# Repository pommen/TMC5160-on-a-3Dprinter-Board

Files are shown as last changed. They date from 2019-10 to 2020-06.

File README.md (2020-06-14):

# TMC5160 on a 3Dprinter Board
 TMC5160 using the pinheaders on a typical 3d printer controllerboard as inputs via an adapter board to a bigger general purpose tmc5160 50V 3-5A (Goal)

All files made in KICAD
(Work in progress)

todo:
bad footprint on RJ45 conn.
Clean up BOM (values and voltages)
74xx125 buffer footprint to wide
bigger fuse footprint (Automotive fuseholder?)
THT caps for H-bridge?
RJ45 pinout on silk?
clearer pin1 marking on 74xx125 buffers
Larger diameter holes on testpoints
I/O testpoints
Diag pin outputs

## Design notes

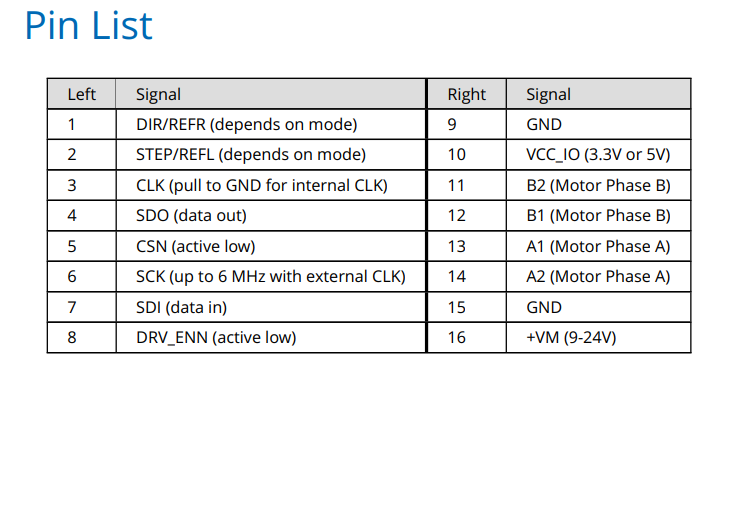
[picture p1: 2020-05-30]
Stepstick pinout.png

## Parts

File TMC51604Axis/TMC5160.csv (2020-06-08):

Id | Designator | Package | Quantity | Designation | Supplier and ref
1 | C37 | C_0805_peter | 1 | 15pF
2 | TP2,TP1 | TestPoint_Pad_D1.5mm | 2 | TestPoint
3 | TP7 | TestPoint_THTPad_1.5x1.5mm_Drill0.7mm | 1 | TestPoint
4 | R52,R51,R27,R16 | R_1206_3216Metric | 4 | 0R1
5 | C47,C46,C45,C44,C43 | C_0805_peter | 5 | 100n
6 | R50 | R_0805_peter | 1 | 20R
7 | C8 | C_2010_5025Metric_Pad1.52x2.65mm_HandSolder | 1 | 47u/25
8 | TP6,TP5,TP4 | TestPoint_Pad_1.5x1.5mm | 3 | TestPoint
9 | C42 | C_0805_peter | 1 | 10u
10 | U3 | LQFP-48-1EP_7x7mm_P0.5mm_EP3.6x3.6mm_peter | 1 | TMC5160A-TA
11 | C34,C9,C27,C33,C41 | C_0603_1608Metric | 5 | 100n
12 | R18,R3 | R_0805_peter | 2 | 100k
13 | R19 | R_0805_peter | 1 | NC
14 | U4 | Oscillator_SMD_Abracon_ASDMB-4Pin_2.5x2.0mm | 1 | ASDMB-12.0MHz
15 | J4 | TerminalBlock_Phoenix_PT-1,5-3-3.5-H_1x03_P3.50mm_Horizontal | 1 | EncCon1
16 | U5,U7,U6 | SO-14_5.3x10.2mm_P1.27mm | 3 | 74LVC125
17 | D27,D29,D28,D26,D25,D24,D23,D22,D21,D20 | SOT-23 | 10 | BAT54S
18 | R49,R48,R40,R39,R38,R37,R36,R35,R34,R33 | R_0805_peter | 10 | 100R
19 | R47,R46,R45,R44,R43,R42,R41,R32,R31,R6 | R_0805_peter | 10 | 2k2
20 | R7 | R_0805_peter | 1 | 1R
21 | R4 | R_0805_peter | 1 | 10K
22 | R5 | R_0805_peter | 1 | 4K12
23 | R2 | R_0805_peter | 1 | 36K5
24 | TP3 | TestPoint_THTPad_1.0x1.0mm_Drill0.5mm | 1 | spare
25 | C18 | C_0805_peter | 1 | 100n/100V
26 | C14 | C_0805_peter | 1 | 22nF
27 | C13 | C_0805_peter | 1 | 220p
28 | C12 | C_0805_peter | 1 | 100p
29 | C11 | C_0805_peter | 1 | 1uF
30 | C6 | C_0805_peter | 1 | 2.2uF
31 | C5 | C_0805_peter | 1 | 47nF
32 | C2 | C_0805_peter | 1 | 10p
33 | C1 | C_0805_peter | 1 | 330n
34 | C10 | C_0603_1608Metric | 1 | 10u
35 | C17 | C_0603_1608Metric | 1 | 22n/100v
36 | C19 | C_0603_1608Metric | 1 | 220n/100v
37 | C22,C24,C26,C35,C36 | C_0603_1608Metric | 5 | 470n
38 | C23 | C_0603_1608Metric | 1 | 2.2uF
39 | C25 | C_0603_1608Metric | 1 | 2.2u
40 | C32,C40 | C_0603_1608Metric | 2 | 2n2
41 | C28,C29,C30,C31 | C_0603_1608Metric | 4 | 1n/100V
42 | U2 | SOT-223-3_TabPin2 | 1 | LM2937
43 | U1 | SOT-23-5_HandSoldering | 1 | AP2210-3.3V
44 | R30,R29 | R_0603_1608Metric | 2 | 100K
45 | R28,R26,R17,R15 | R_0603_1608Metric | 4 | 47R
46 | R25,R24,R23,R22,R14,R13,R11,R10 | R_0603_1608Metric | 8 | 12R
47 | R21,R20,R12,R9 | R_0603_1608Metric | 4 | 0R
48 | R8 | R_0603_1608Metric | 1 | 2R2
49 | R1 | R_2512_6332Metric | 1 | 0R01
50 | Q4 | SOT-23 | 1 | BSS138
51 | Q3,Q2 | V-DFN5045-12 | 2 | DMHT6016LFJ
52 | Q1 | TO-252-2 | 1 | SUD08P06-155L
53 | L1 | L_7.3x7.3_H3.5 | 1 | 33uH
54 | JP3 | SolderJumper-3_P2.0mm_Open_TrianglePad1.0x1.5mm | 1 | Encoder_Voltage_Sel
55 | JP2 | SolderJumper-3_P2.0mm_Open_TrianglePad1.0x1.5mm | 1 | SD_MODE
56 | JP1 | SolderJumper-3_P2.0mm_Open_TrianglePad1.0x1.5mm | 1 | SPI_MODE
57 | J6 | TerminalBlock_Phoenix_PT-1,5-3-3.5-H_1x03_P3.50mm_Horizontal | 1 | EncCon2
58 | J5,J3 | 360s-1812-11001(RJ45) | 2 | RJ45_Shielded
59 | J2 | TerminalBlock_Phoenix_PT-1,5-4-3.5-H_1x04_P3.50mm_Horizontal | 1 | Stepper_conn
60 | J1 | PhoenixContact_MSTB_2,5_2-GF_1x02_P5.00mm_Horizontal_ThreadedFlange_MountHole | 1 | +48Vin
61 | H4,H3,H2,H1 | MountingHole_3.2mm_M3 | 4 | MountingHole
62 | FB2 | R_0805_2012Metric_Pad1.15x1.40mm_HandSolder | 1 | MPZ2012S601A
63 | F1 | Fuse_2512_6332Metric | 1 | Fuse
64 | D19,D18,D17,D16,D15,D14,D13,D12,D11 | D_0805__HandSolder_peter | 9 | LED
65 | D10,D9,D8,D7 | SOT-23 | 4 | ZHCS1006TA
66 | D6 | D_SOD-123F | 1 | D_Schottky
67 | D5 | TSSOP-16-1EP_4.4x5mm_P0.65mm | 1 | LT1766
68 | D4 | D_0805_2012Metric | 1 | LED
69 | D3 | D_1206_3216Metric | 1 | 10V
70 | D2 | D_1206_3216Metric | 1 | 7V
71 | D1 | D_SOD-123 | 1 | 1N4148W
72 | C39,C21 | CP_Elec_10x14.3 | 2 | 220uF/100V
73 | C38,C20 | C_1206_3216Metric | 2 | 470n/100V
74 | C16 | C_1210_3225Metric_Pad1.42x2.65mm_HandSolder | 1 | 4,7uF/100v
75 | C15 | C_1210_3225Metric_Pad1.42x2.65mm_HandSolder | 1 | 100n/100v
76 | C7 | CP_Radial_D10.0mm_P5.00mm | 1 | 47u/25V
77 | C4 | CP_Elec_8x6.2 | 1 | 22uF/100v
78 | C3 | CP_Elec_8x6.2 | 1 | 10uF/100v

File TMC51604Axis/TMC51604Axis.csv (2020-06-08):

Source: | E:\GitHub\TMC5160 on a 3Dprinter Board\TMC5160-on-a-3Dprinter-Board\TMC51604Axis\TMC51604Axis.sch
Date: | 06/01/20 14:39:34
Tool: | Eeschema (5.1.6)-1
Generator: | C:\Program Files\KiCad\bin\scripting\plugins/bom_csv_grouped_by_value_with_fp.py
Component Count: | 162
Ref | Qnty | Value | Cmp name | Footprint | Description | Vendor
C1, | 1 | 330n | C_Small | peters:C_0805_peter | Unpolarized capacitor, small symbol
C2, | 1 | 10p | C_Small | peters:C_0805_peter | Unpolarized capacitor, small symbol
C3, | 1 | 10uF/100v | CP | Capacitor_SMD:CP_Elec_8x6.2 | Polarized capacitor
C4, | 1 | 22uF/100v | C | Capacitor_SMD:CP_Elec_8x6.2 | Unpolarized capacitor
C5, | 1 | 47nF | C | peters:C_0805_peter | Unpolarized capacitor
C6, | 1 | 2.2uF | C | peters:C_0805_peter | Unpolarized capacitor
C7, | 1 | 47u/25V | CP | Capacitor_THT:CP_Radial_D10.0mm_P5.00mm | Polarized capacitor
C8, | 1 | 47u/25 | C | Capacitor_SMD:C_2010_5025Metric_Pad1.52x2.65mm_HandSolder | Unpolarized capacitor
C9, C27, C33, C34, C41, | 5 | 100n | C_Small | Capacitor_SMD:C_0603_1608Metric | Unpolarized capacitor, small symbol
C10, | 1 | 10u | C | Capacitor_SMD:C_0603_1608Metric | Unpolarized capacitor
C11, | 1 | 1uF | C | peters:C_0805_peter | Unpolarized capacitor
C12, | 1 | 100p | C | peters:C_0805_peter | Unpolarized capacitor
C13, | 1 | 220p | C | peters:C_0805_peter | Unpolarized capacitor
C14, | 1 | 22nF | C_Small | peters:C_0805_peter | Unpolarized capacitor, small symbol
C15, | 1 | 100n/100v | C_Small | Capacitor_SMD:C_1210_3225Metric_Pad1.42x2.65mm_HandSolder | Unpolarized capacitor, small symbol
C16, | 1 | 4,7uF/100v | C_Small | Capacitor_SMD:C_1210_3225Metric_Pad1.42x2.65mm_HandSolder | Unpolarized capacitor, small symbol
C17, | 1 | 22n/100v | C_Small | Capacitor_SMD:C_0603_1608Metric | Unpolarized capacitor, small symbol
C18, | 1 | 100n/100V | C_Small | peters:C_0805_peter | Unpolarized capacitor, small symbol
C19, | 1 | 220n/100v | C_Small | Capacitor_SMD:C_0603_1608Metric | Unpolarized capacitor, small symbol
C20, C38, | 2 | 470n/100V | C | Capacitor_SMD:C_1206_3216Metric | Unpolarized capacitor
C21, C39, | 2 | 220uF/100V | CP | Capacitor_SMD:CP_Elec_10x14.3 | Polarized capacitor
C22, C24, C26, C35, C36, | 5 | 470n | C_Small | Capacitor_SMD:C_0603_1608Metric | Unpolarized capacitor, small symbol
C23, | 1 | 2.2uF | C_Small | Capacitor_SMD:C_0603_1608Metric | Unpolarized capacitor, small symbol
C25, | 1 | 2.2u | C_Small | Capacitor_SMD:C_0603_1608Metric | Unpolarized capacitor, small symbol
C28, C29, C30, C31, | 4 | 1n/100V | C | Capacitor_SMD:C_0603_1608Metric | Unpolarized capacitor
C32, C40, | 2 | 2n2 | C_Small | Capacitor_SMD:C_0603_1608Metric | Unpolarized capacitor, small symbol
C37, | 1 | 15pF | C | peters:D_0805_peter | Unpolarized capacitor
C42, | 1 | 10u | C | peters:C_0805_peter | Unpolarized capacitor
C43, C44, C45, C46, C47, | 5 | 100n | C | peters:C_0805_peter | Unpolarized capacitor
D1, | 1 | 1N4148W | 1N4148W | Diode_SMD:D_SOD-123 | 75V 0.15A Fast Switching Diode, SOD-123
D2, | 1 | 7V | D_Zener | Diode_SMD:D_1206_3216Metric | Zener diode
D3, | 1 | 10V | D_Zener | Diode_SMD:D_1206_3216Metric | Zener diode
D4, | 1 | LED | LED | Diode_SMD:D_0805_2012Metric | Light emitting diode
D5, | 1 | LT1766 | LT1766 | Package_SO:TSSOP-16-1EP_4.4x5mm_P0.65mm | 5.5V to 60V 1.5A, 200kHz Step-Down Switching Regulator
D6, | 1 | D_Schottky | D_Schottky | Diode_SMD:D_SOD-123F | Schottky diode
D7, D8, D9, D10, | 4 | ZHCS1006TA | ZHCS1006TA | Package_TO_SOT_SMD:SOT-23
D11, D12, D13, D14, D15, D16, D17, D18, D19, | 9 | LED | LED | peters:D_0805__HandSolder_peter | Light emitting diode
D20, D21, D22, D23, D24, D25, D26, D27, D28, D29, | 10 | BAT54S | BAT54S | Package_TO_SOT_SMD:SOT-23 | schottky barrier diode
F1, | 1 | Fuse | Fuse | Fuse:Fuse_2512_6332Metric | Fuse
FB2, | 1 | MPZ2012S601A | Ferrite_Bead | Resistor_SMD:R_0805_2012Metric_Pad1.15x1.40mm_HandSolder | Ferrite bead
H1, H2, H3, H4, | 4 | MountingHole | MountingHole | MountingHole:MountingHole_3.2mm_M3 | Mounting Hole without connection
J1, | 1 | +48Vin | Conn_01x02_Female | Connector_Phoenix_MSTB:PhoenixContact_MSTB_2,5_2-GF_1x02_P5.00mm_Horizontal_ThreadedFlange_MountHole | Generic connector, single row, 01x02, script generated (kicad-library-utils/schlib/autogen/connector/)
J2, | 1 | Stepper_conn | Screw_Terminal_01x04 | TerminalBlock_Phoenix:TerminalBlock_Phoenix_PT-1,5-4-3.5-H_1x04_P3.50mm_Horizontal | Generic screw terminal, single row, 01x04, script generated (kicad-library-utils/schlib/autogen/connector/)
J3, J5, | 2 | RJ45_Shielded | RJ45_Shielded | peters:360s-1812-11001(RJ45) | RJ connector, 8P8C (8 positions 8 connected), Shielded
J4, | 1 | EncCon1 | Screw_Terminal_01x03 | TerminalBlock_Phoenix:TerminalBlock_Phoenix_PT-1,5-3-3.5-H_1x03_P3.50mm_Horizontal | Generic screw terminal, single row, 01x03, script generated (kicad-library-utils/schlib/autogen/connector/)
J6, | 1 | EncCon2 | Screw_Terminal_01x03 | TerminalBlock_Phoenix:TerminalBlock_Phoenix_PT-1,5-3-3.5-H_1x03_P3.50mm_Horizontal | Generic screw terminal, single row, 01x03, script generated (kicad-library-utils/schlib/autogen/connector/)
JP1, | 1 | SPI_MODE | Jumper_NC_Dual | Jumper:SolderJumper-3_P2.0mm_Open_TrianglePad1.0x1.5mm | Dual jumper, normally closed
JP2, | 1 | SD_MODE | Jumper_NC_Dual | Jumper:SolderJumper-3_P2.0mm_Open_TrianglePad1.0x1.5mm | Dual jumper, normally closed
JP3, | 1 | Encoder_Voltage_Sel | Jumper_3_Bridged12 | Jumper:SolderJumper-3_P2.0mm_Open_TrianglePad1.0x1.5mm | Jumper, 3-pole, pins 1+2 closed/bridged
L1, | 1 | 33uH | L | Inductor_SMD:L_7.3x7.3_H3.5 | Inductor
Q1, | 1 | SUD08P06-155L | SUD08P06-155L | Package_TO_SOT_SMD:TO-252-2 | 8.4A Id, 60V Vds, TrenchFET P-Channel Power MOSFET, 155mOhm Ron, 19nC Qg, -55 to 150 °C, TO-252-2
Q2, Q3, | 2 | DMHT6016LFJ | DMHT6016LFJ | Libs:V-DFN5045-12 | 60V N-CHANNEL ENHANCEMENT MODE MOSFET H-BRIDGE
Q4, | 1 | BSS138 | BSS138 | Package_TO_SOT_SMD:SOT-23 | 50V Vds, 0.22A Id, N-Channel MOSFET, SOT-23
R1, | 1 | 0R01 | R | Resistor_SMD:R_2512_6332Metric | Resistor
R2, | 1 | 36K5 | R_Small | peters:R_0805_peter | Resistor, small symbol
R3, R18, | 2 | 100k | R | peters:R_0805_peter | Resistor
R4, | 1 | 10K | R | peters:R_0805_peter | Resistor
R5, | 1 | 4K12 | R_Small | peters:R_0805_peter | Resistor, small symbol
R6, R31, R32, R41, R42, R43, R44, R45, R46, R47, | 10 | 2k2 | R | peters:R_0805_peter | Resistor
R7, | 1 | 1R | R_Small | peters:R_0805_peter | Resistor, small symbol
R8, | 1 | 2R2 | R_Small | Resistor_SMD:R_0603_1608Metric | Resistor, small symbol
R9, R12, R20, R21, | 4 | 0R | R_Small | Resistor_SMD:R_0603_1608Metric | Resistor, small symbol
R10, R11, R13, R14, R22, R23, R24, R25, | 8 | 12R | R_Small | Resistor_SMD:R_0603_1608Metric | Resistor, small symbol
R15, R17, R26, R28, | 4 | 47R | R | Resistor_SMD:R_0603_1608Metric | Resistor
R16, R27, R51, R52, | 4 | 0R1 | R | Resistor_SMD:R_1206_3216Metric | Resistor
R19, | 1 | NC | R | peters:R_0805_peter | Resistor
R29, R30, | 2 | 100K | R_Small | Resistor_SMD:R_0603_1608Metric | Resistor, small symbol
R33, R34, R35, R36, R37, R38, R39, R40, R48, R49, | 10 | 100R | R | peters:R_0805_peter | Resistor
R50, | 1 | 20R | R | peters:R_0805_peter | Resistor
TP1, TP2, | 2 | TestPoint | TestPoint | TestPoint:TestPoint_Pad_D1.5mm | test point
TP3, | 1 | spare | TestPoint | TestPoint:TestPoint_THTPad_1.0x1.0mm_Drill0.5mm | test point
TP4, TP5, TP6, | 3 | TestPoint | TestPoint | TestPoint:TestPoint_Pad_1.5x1.5mm | test point
TP7, | 1 | TestPoint | TestPoint | TestPoint:TestPoint_THTPad_1.5x1.5mm_Drill0.7mm | test point
U1, | 1 | AP2210-3.3V | AP2210-3.3V | Package_TO_SOT_SMD:SOT-23-5_HandSoldering | AP2210 Series 3.3 V 300 mA Surface Mount RF ULDO Regulator - SOT-23-5
U2, | 1 | LM2937 | LM2937 | Package_TO_SOT_SMD:SOT-223-3_TabPin2 | LM2937 500-mA Low Dropout Regulator
U3, | 1 | TMC5160A-TA | TMC5160A-TA | peters:LQFP-48-1EP_7x7mm_P0.5mm_EP3.6x3.6mm_peter | The TMC5160 is a high power stepper motor controller and driver IC with serial communication interfaces
U4, | 1 | ASDMB-12.0MHz | ASDMB-xxxMHz | Oscillator:Oscillator_SMD_Abracon_ASDMB-4Pin_2.5x2.0mm | 1.8-3.3V SMD Ultra Miniature Crystal Clock Oscillator, Abracon
U5, U6, U7, | 3 | 74LVC125 | 74LVC125 | Package_SO:SO-14_5.3x10.2mm_P1.27mm | Quad buffer 3-State outputs

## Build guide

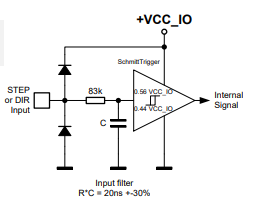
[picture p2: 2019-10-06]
step dir schmitt trig.png

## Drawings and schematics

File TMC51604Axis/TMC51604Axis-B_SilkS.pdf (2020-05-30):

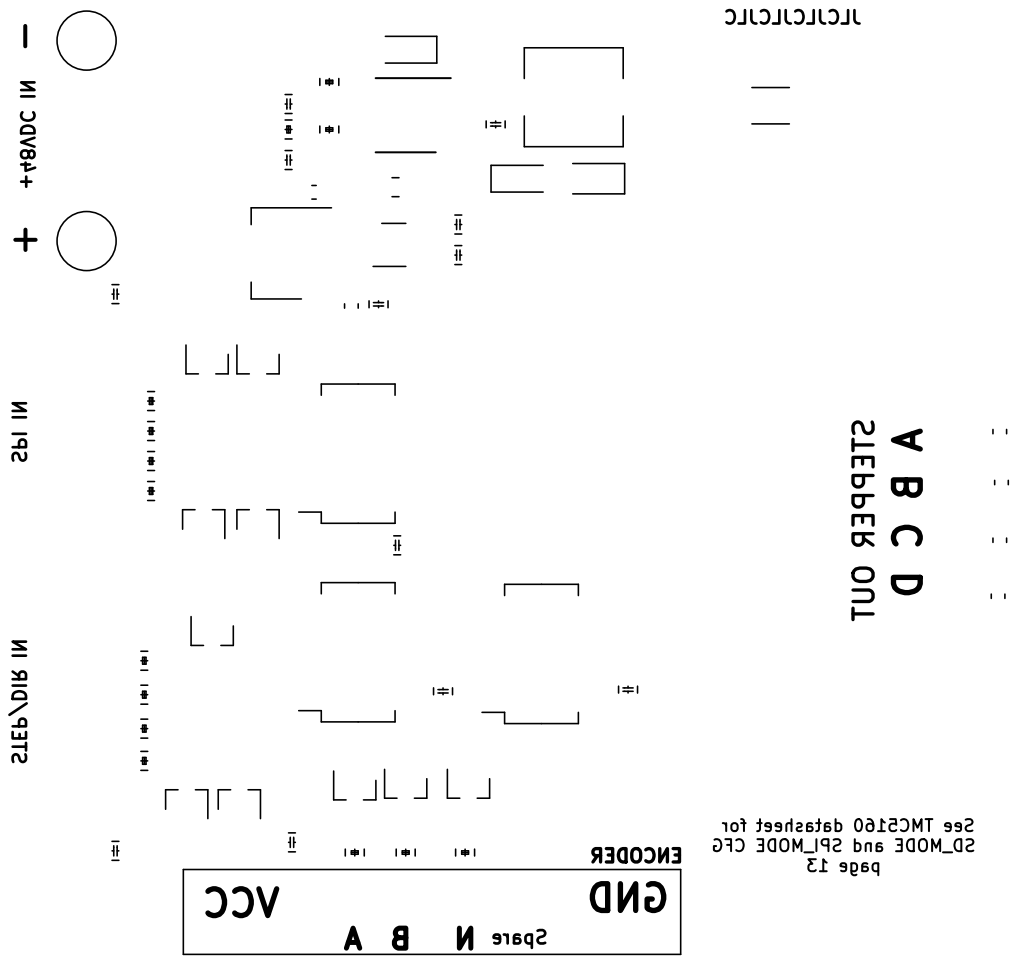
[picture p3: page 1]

page 13 - + GND A B N Spare VCC

ENCODER STEP/DIR IN SPI IN +48VDC IN D C B STEPPER OUT A

See TMC5160 datasheet for SD_MODE and SPI_MODE CFG

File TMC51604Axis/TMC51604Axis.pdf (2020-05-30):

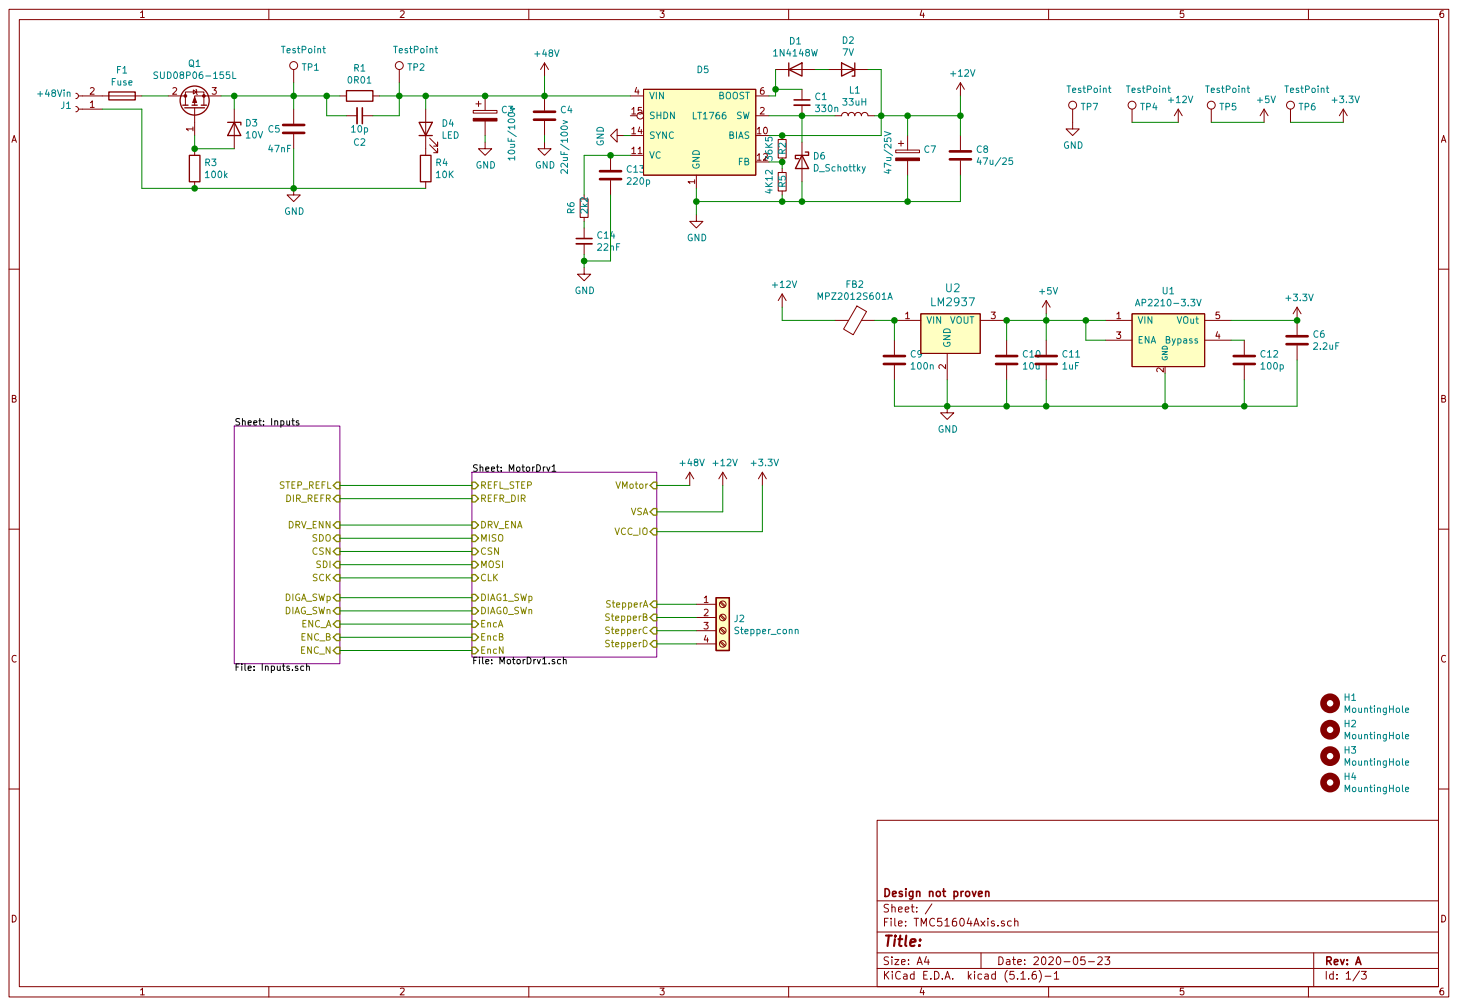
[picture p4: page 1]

1 BIAS 10 VC 11 FB 12 SYNC 14 SHDN 15 SW 2 VIN 4 BOOST 6 D5
TP6 TestPoint C13

2 ENA 3 Bypass 4 VOut 5 U1 AP2210-3.3V GND

Sheet: Inputs
Sheet: MotorDrv1 File: MotorDrv1.sch CLK MOSI MISO
VMotor REFR_DIR

Id: 1/3 Title: File: TMC51604Axis.sch Sheet: / Design not proven

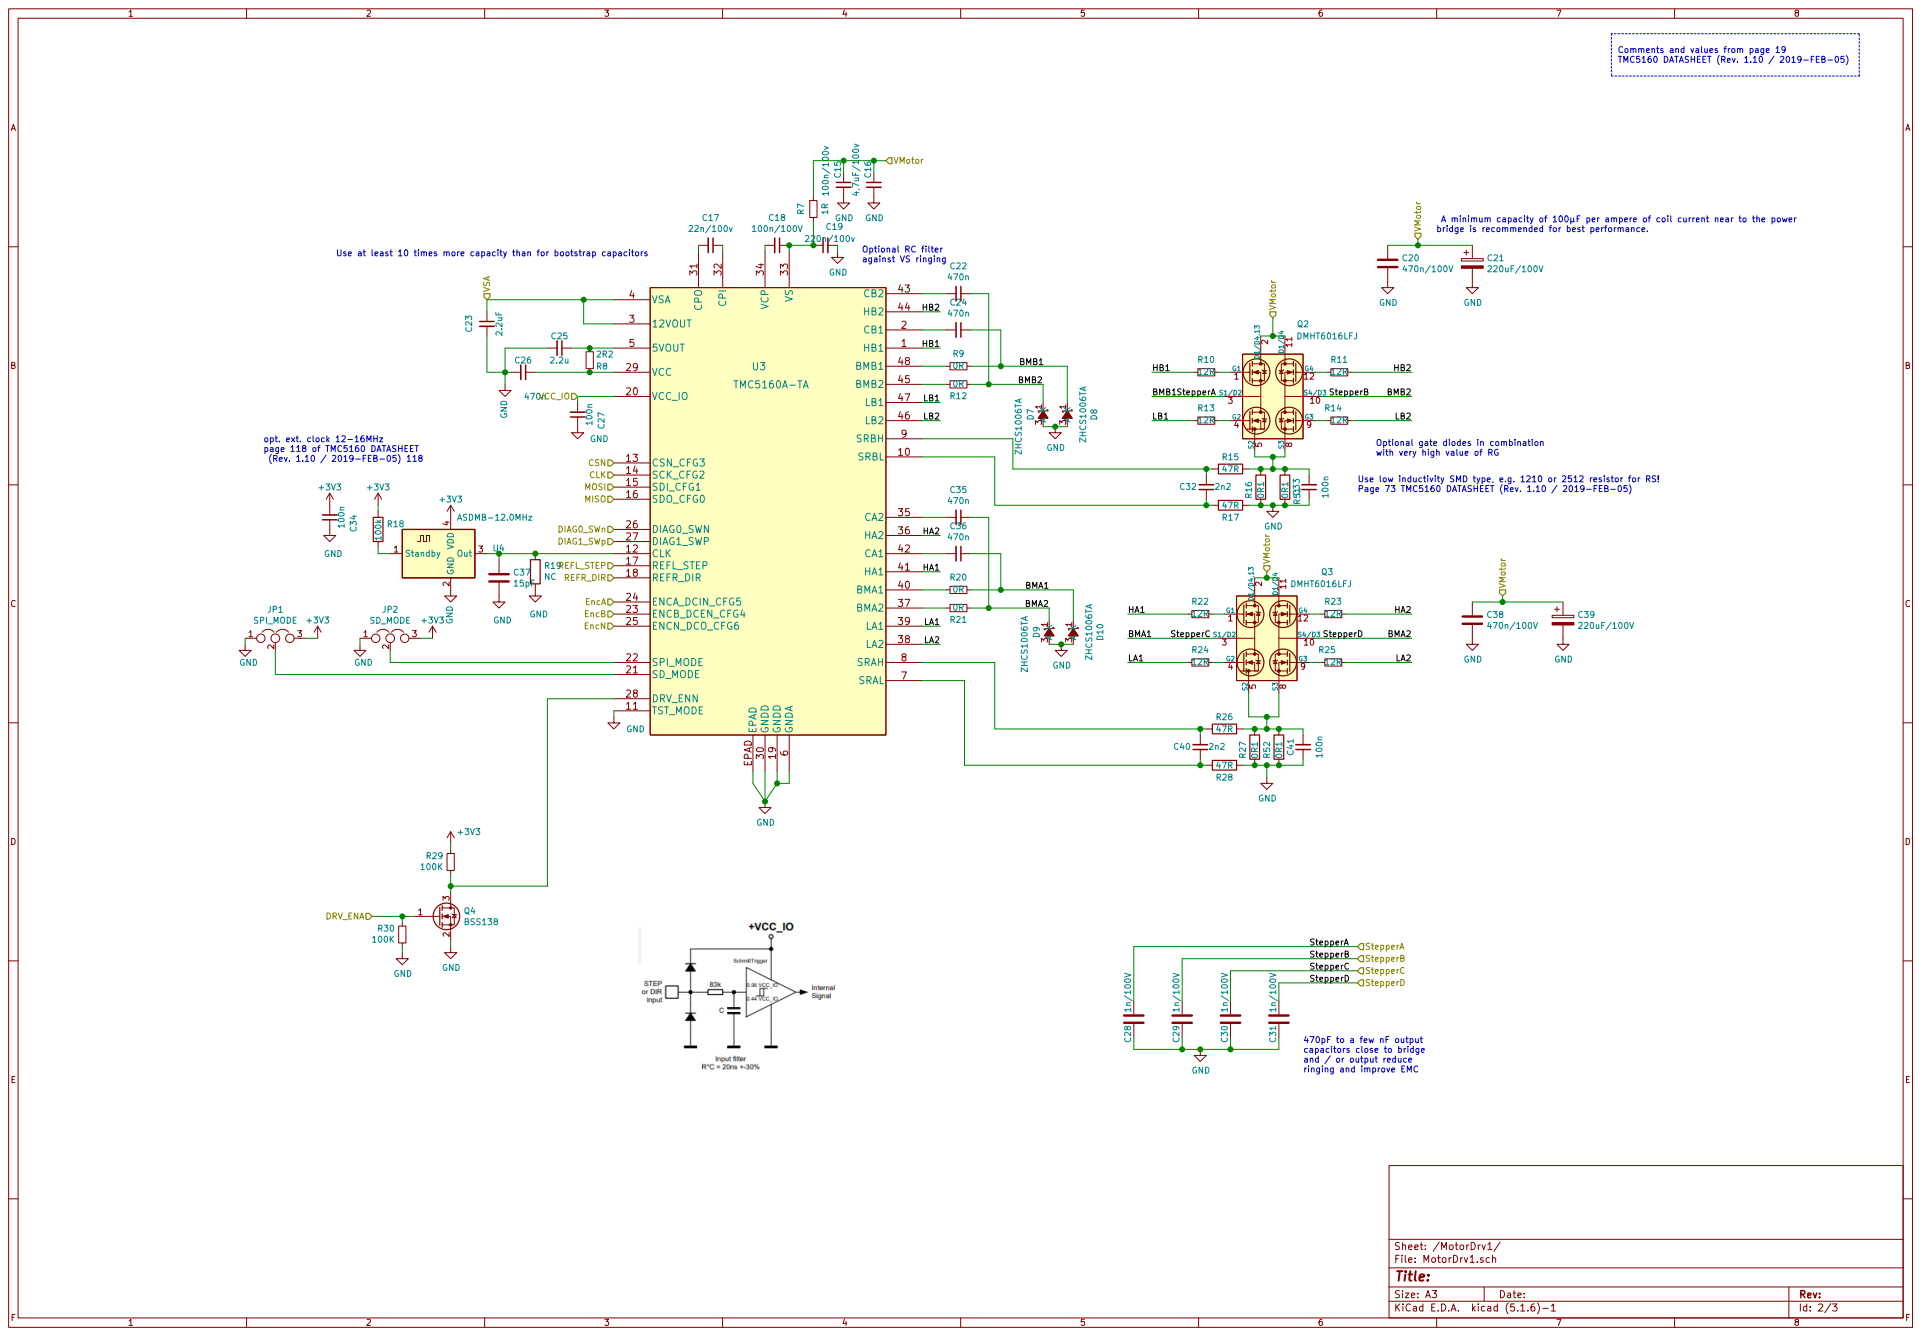
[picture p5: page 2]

Comments and values from page 19
TMC5160 DATASHEET (Rev. 1.10 / 2019-FEB-05)

6 SRAL 7 SRAH 8 SRBH 9 EPAD EPAD U3 TMC5160A-TA C15 100n/100v GND C41 100n

A minimum capacity of 100µF per ampere of coil current near to the power
bridge is recommended for best performance.

Use at least 10 times more capacity than for bootstrap capacitors

Optional gate diodes in combination
with very high value of RG

Page 73 TMC5160 DATASHEET (Rev. 1.10 / 2019-FEB-05)

470pF to a few nF output
capacitors close to bridge
and / or output reduce
ringing and improve EMC

Id: 2/3 Title: File: MotorDrv1.sch Sheet: /MotorDrv1/

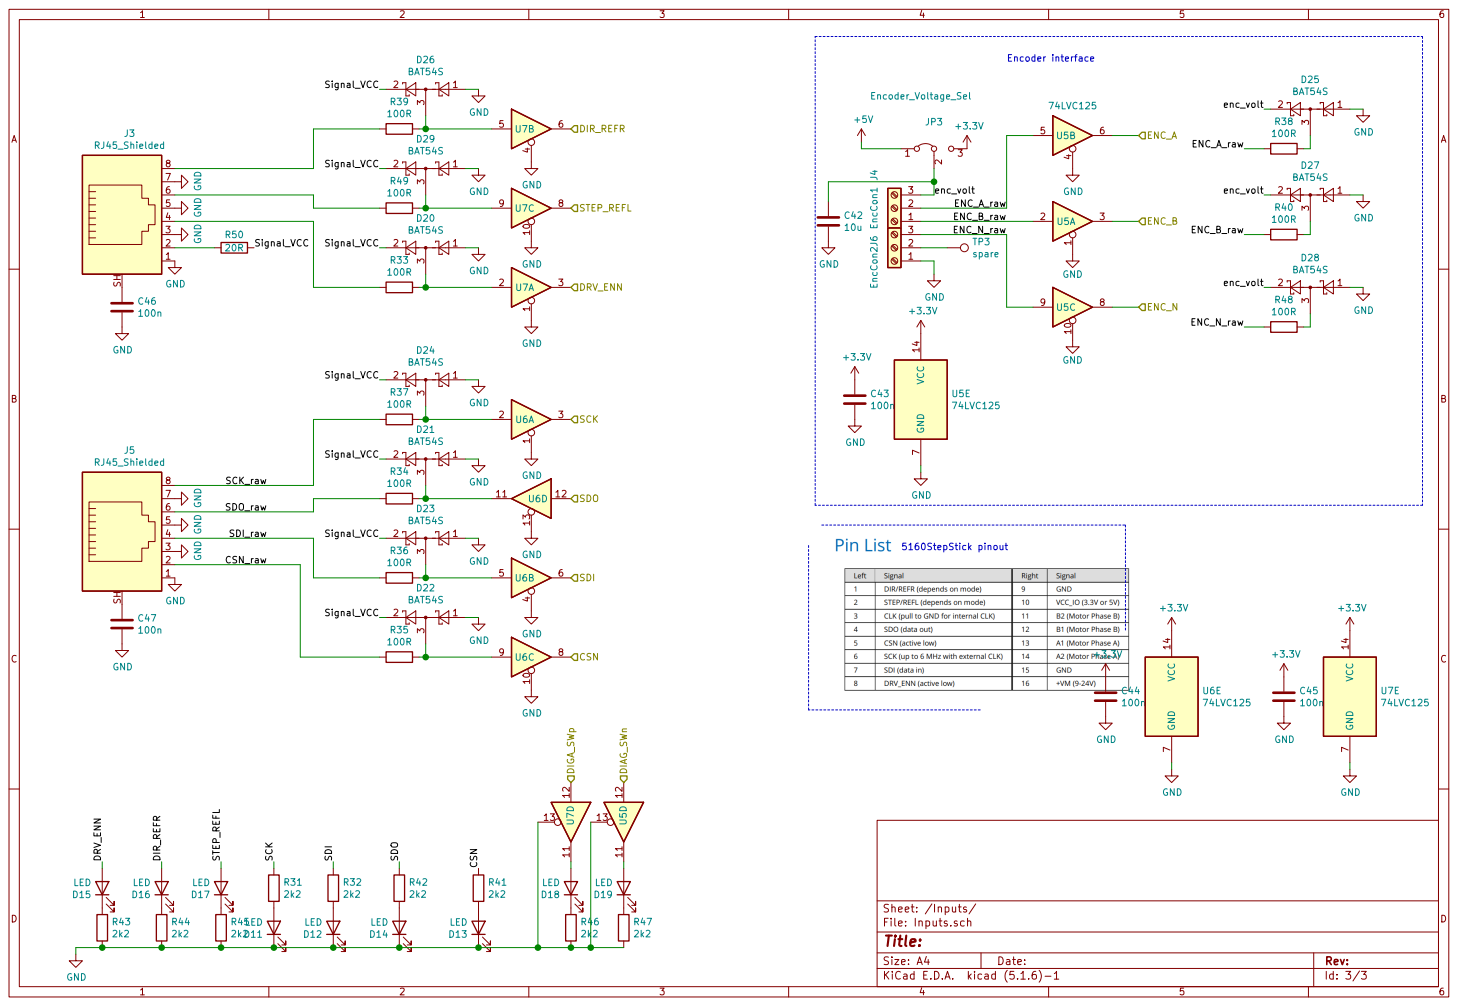
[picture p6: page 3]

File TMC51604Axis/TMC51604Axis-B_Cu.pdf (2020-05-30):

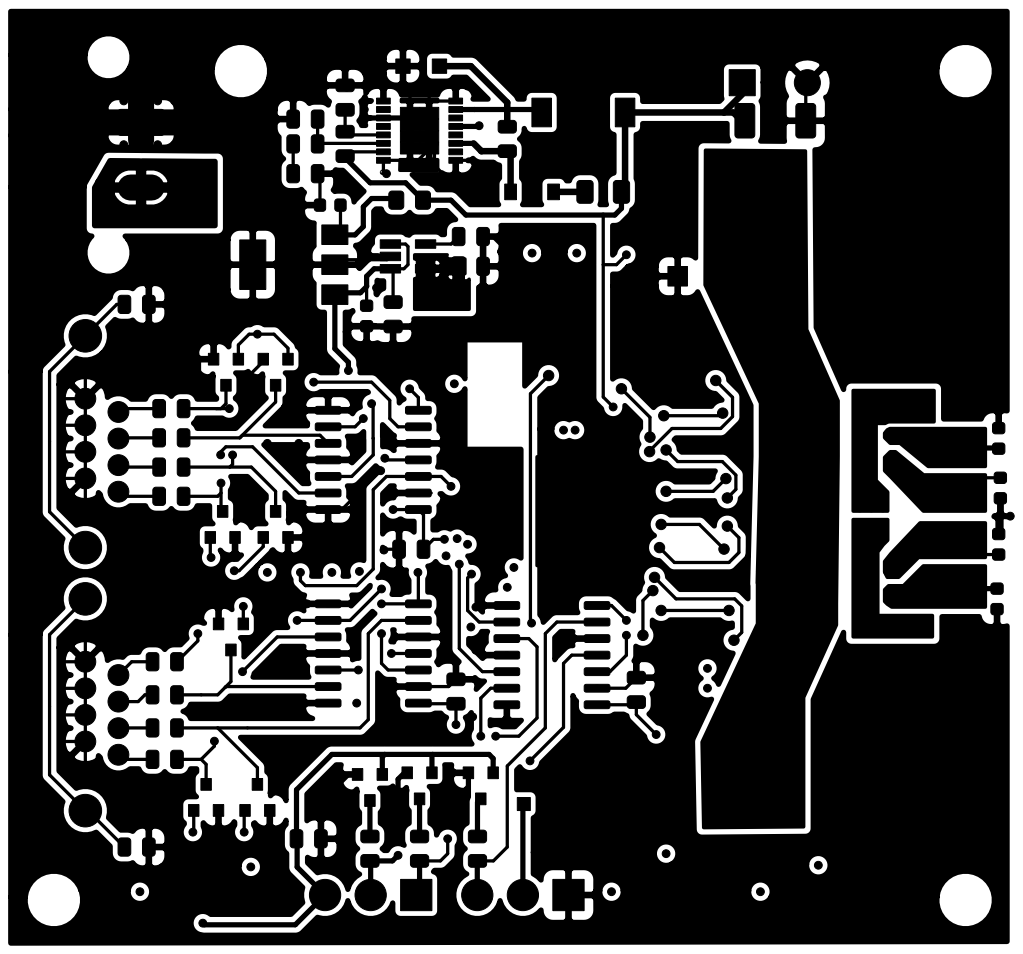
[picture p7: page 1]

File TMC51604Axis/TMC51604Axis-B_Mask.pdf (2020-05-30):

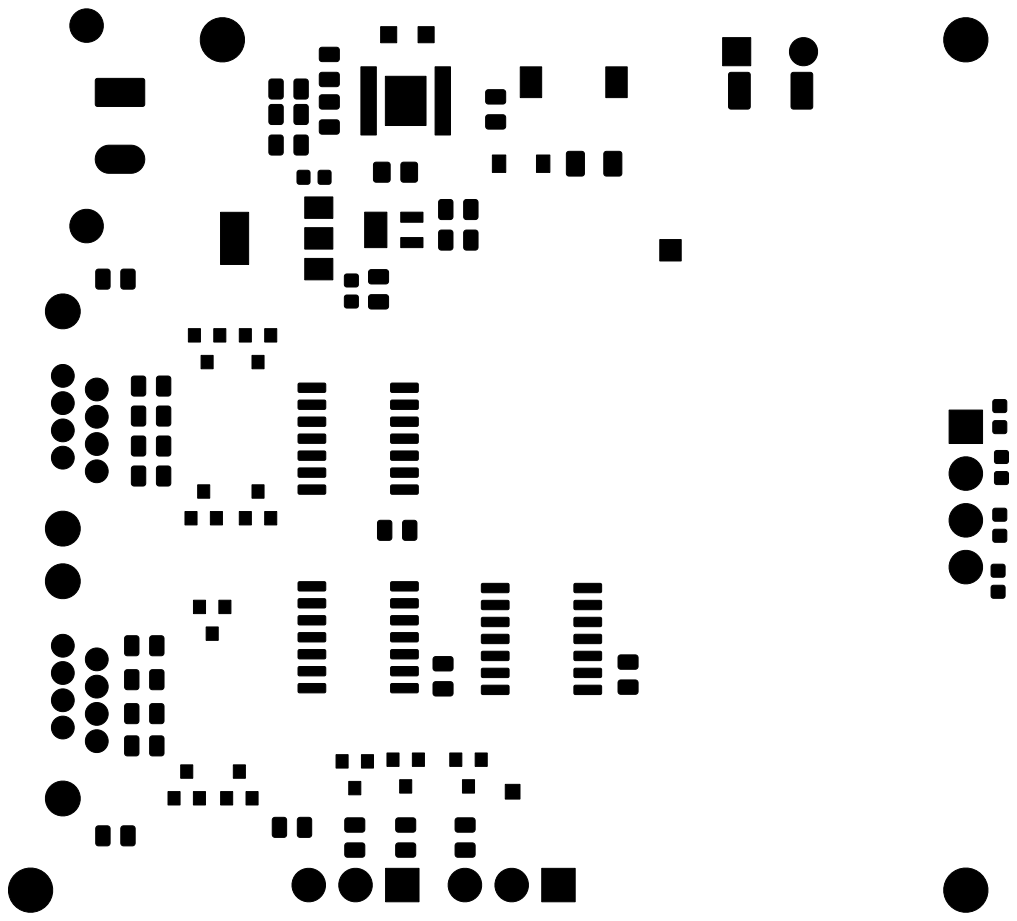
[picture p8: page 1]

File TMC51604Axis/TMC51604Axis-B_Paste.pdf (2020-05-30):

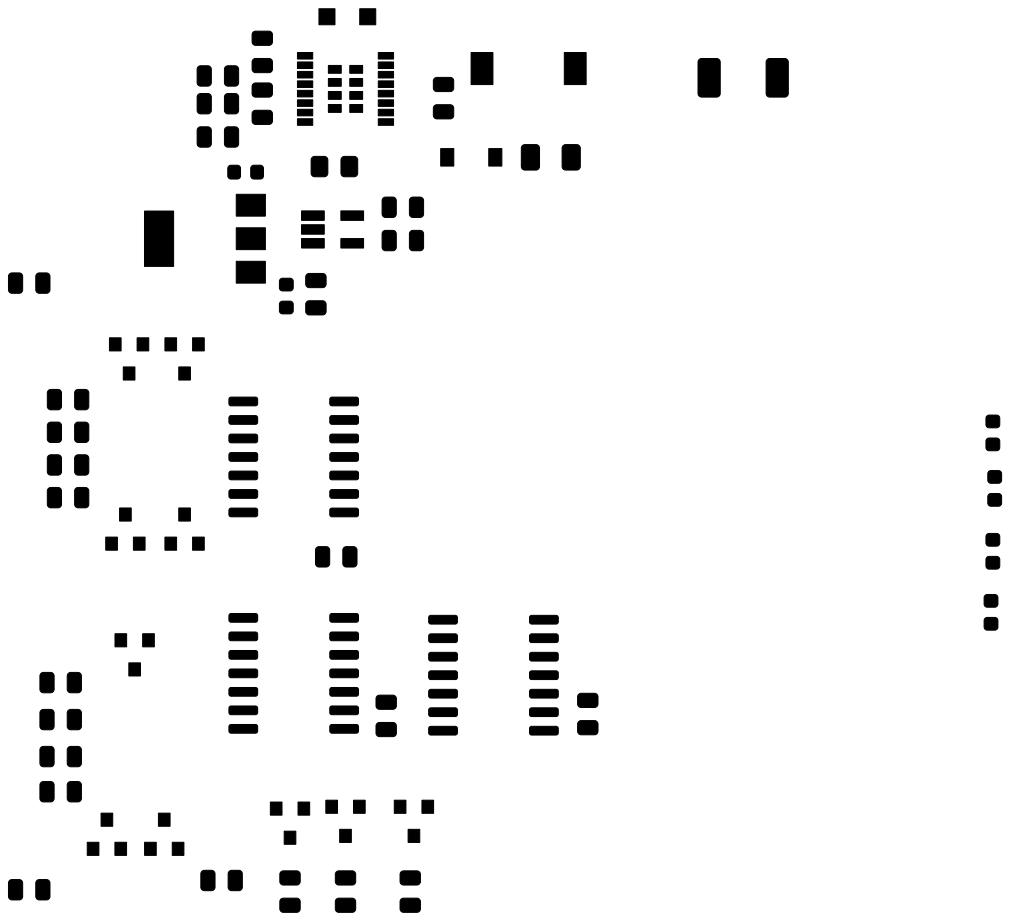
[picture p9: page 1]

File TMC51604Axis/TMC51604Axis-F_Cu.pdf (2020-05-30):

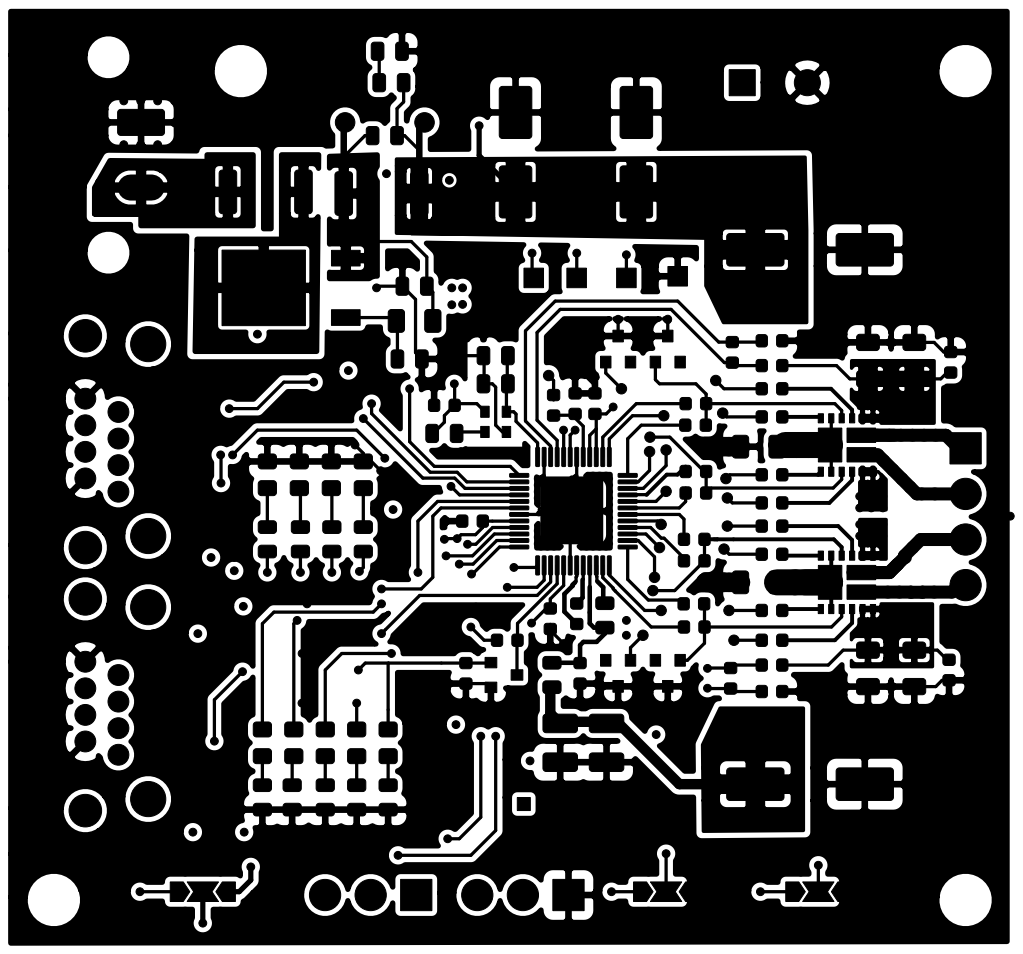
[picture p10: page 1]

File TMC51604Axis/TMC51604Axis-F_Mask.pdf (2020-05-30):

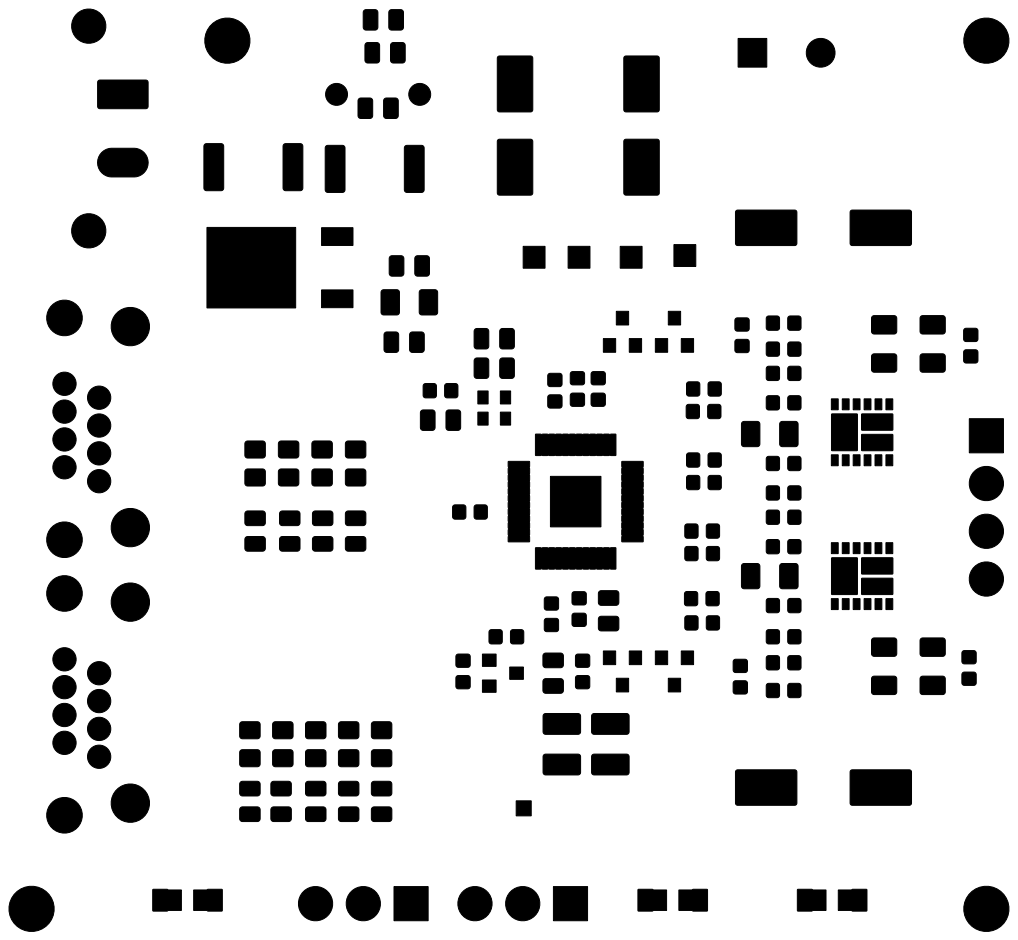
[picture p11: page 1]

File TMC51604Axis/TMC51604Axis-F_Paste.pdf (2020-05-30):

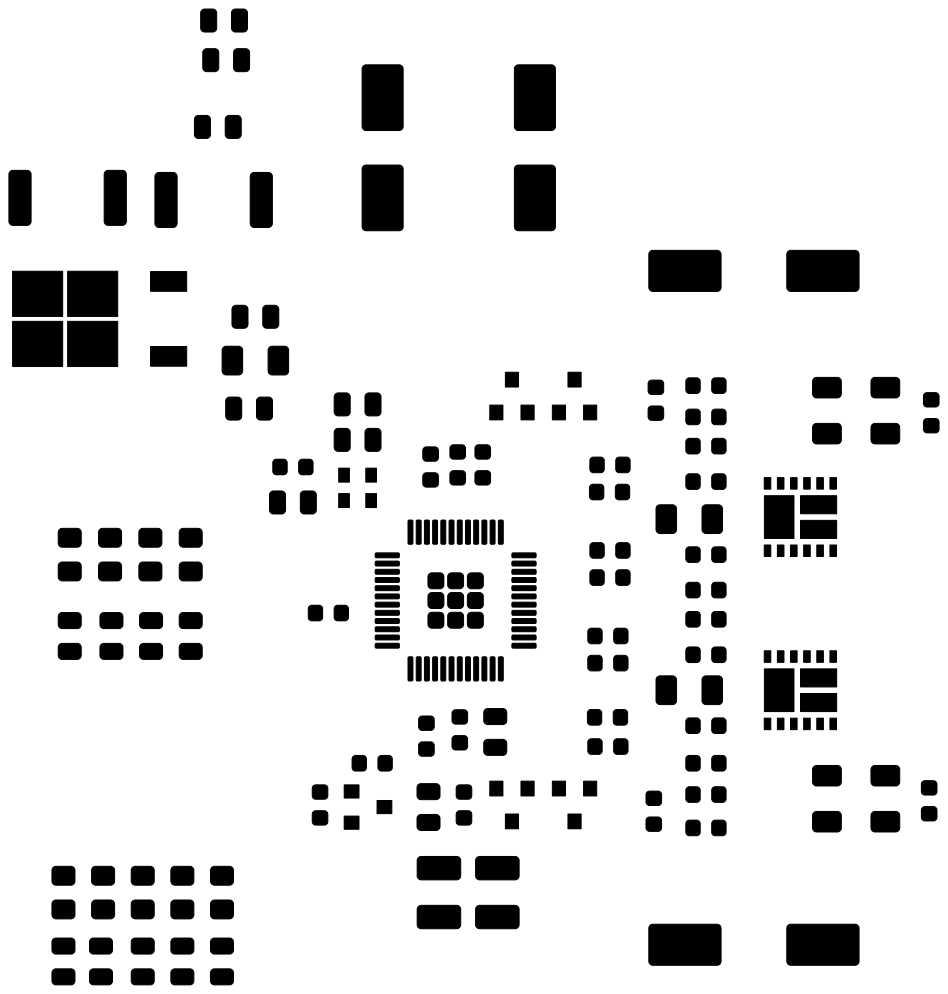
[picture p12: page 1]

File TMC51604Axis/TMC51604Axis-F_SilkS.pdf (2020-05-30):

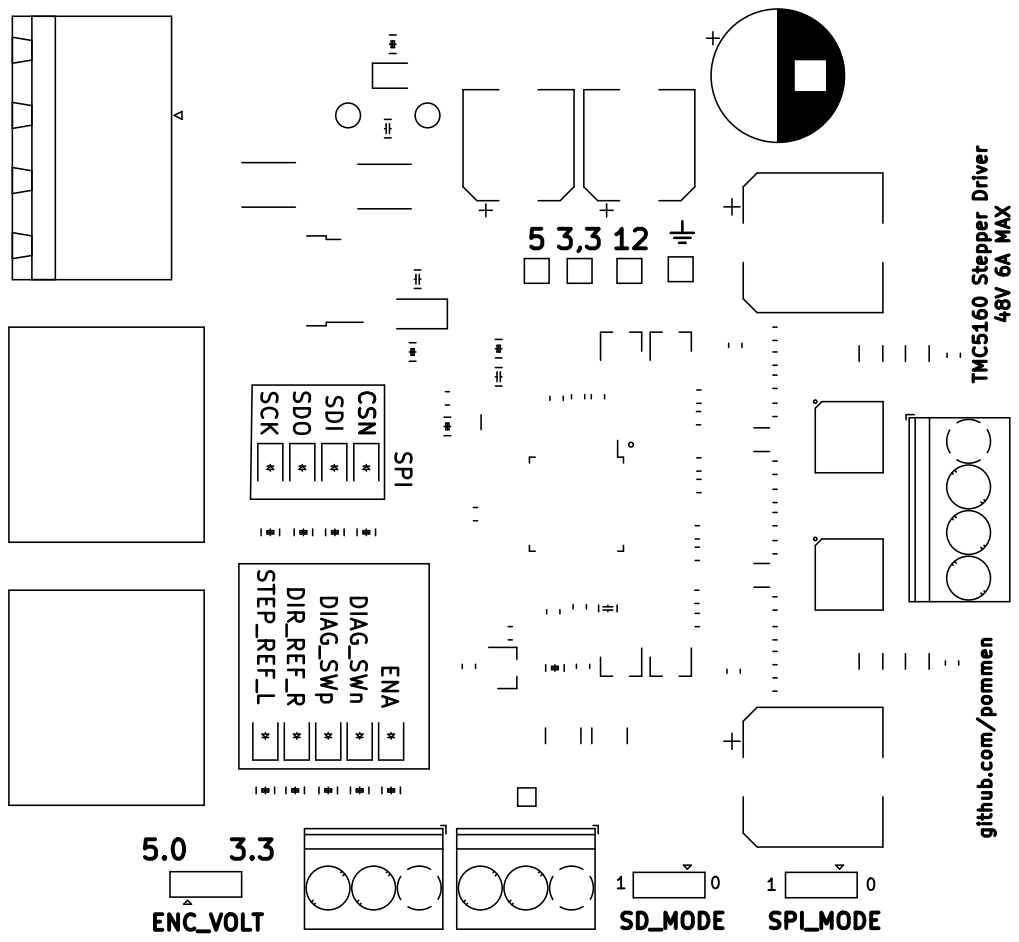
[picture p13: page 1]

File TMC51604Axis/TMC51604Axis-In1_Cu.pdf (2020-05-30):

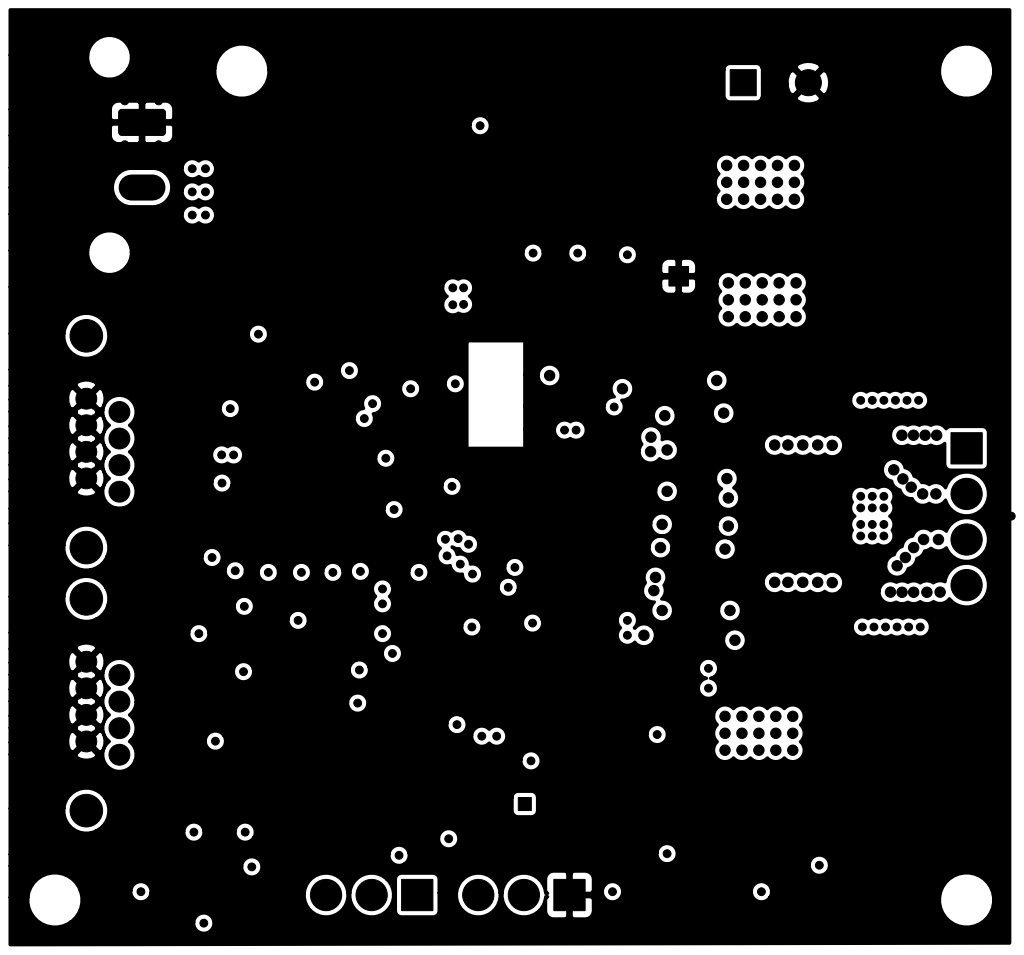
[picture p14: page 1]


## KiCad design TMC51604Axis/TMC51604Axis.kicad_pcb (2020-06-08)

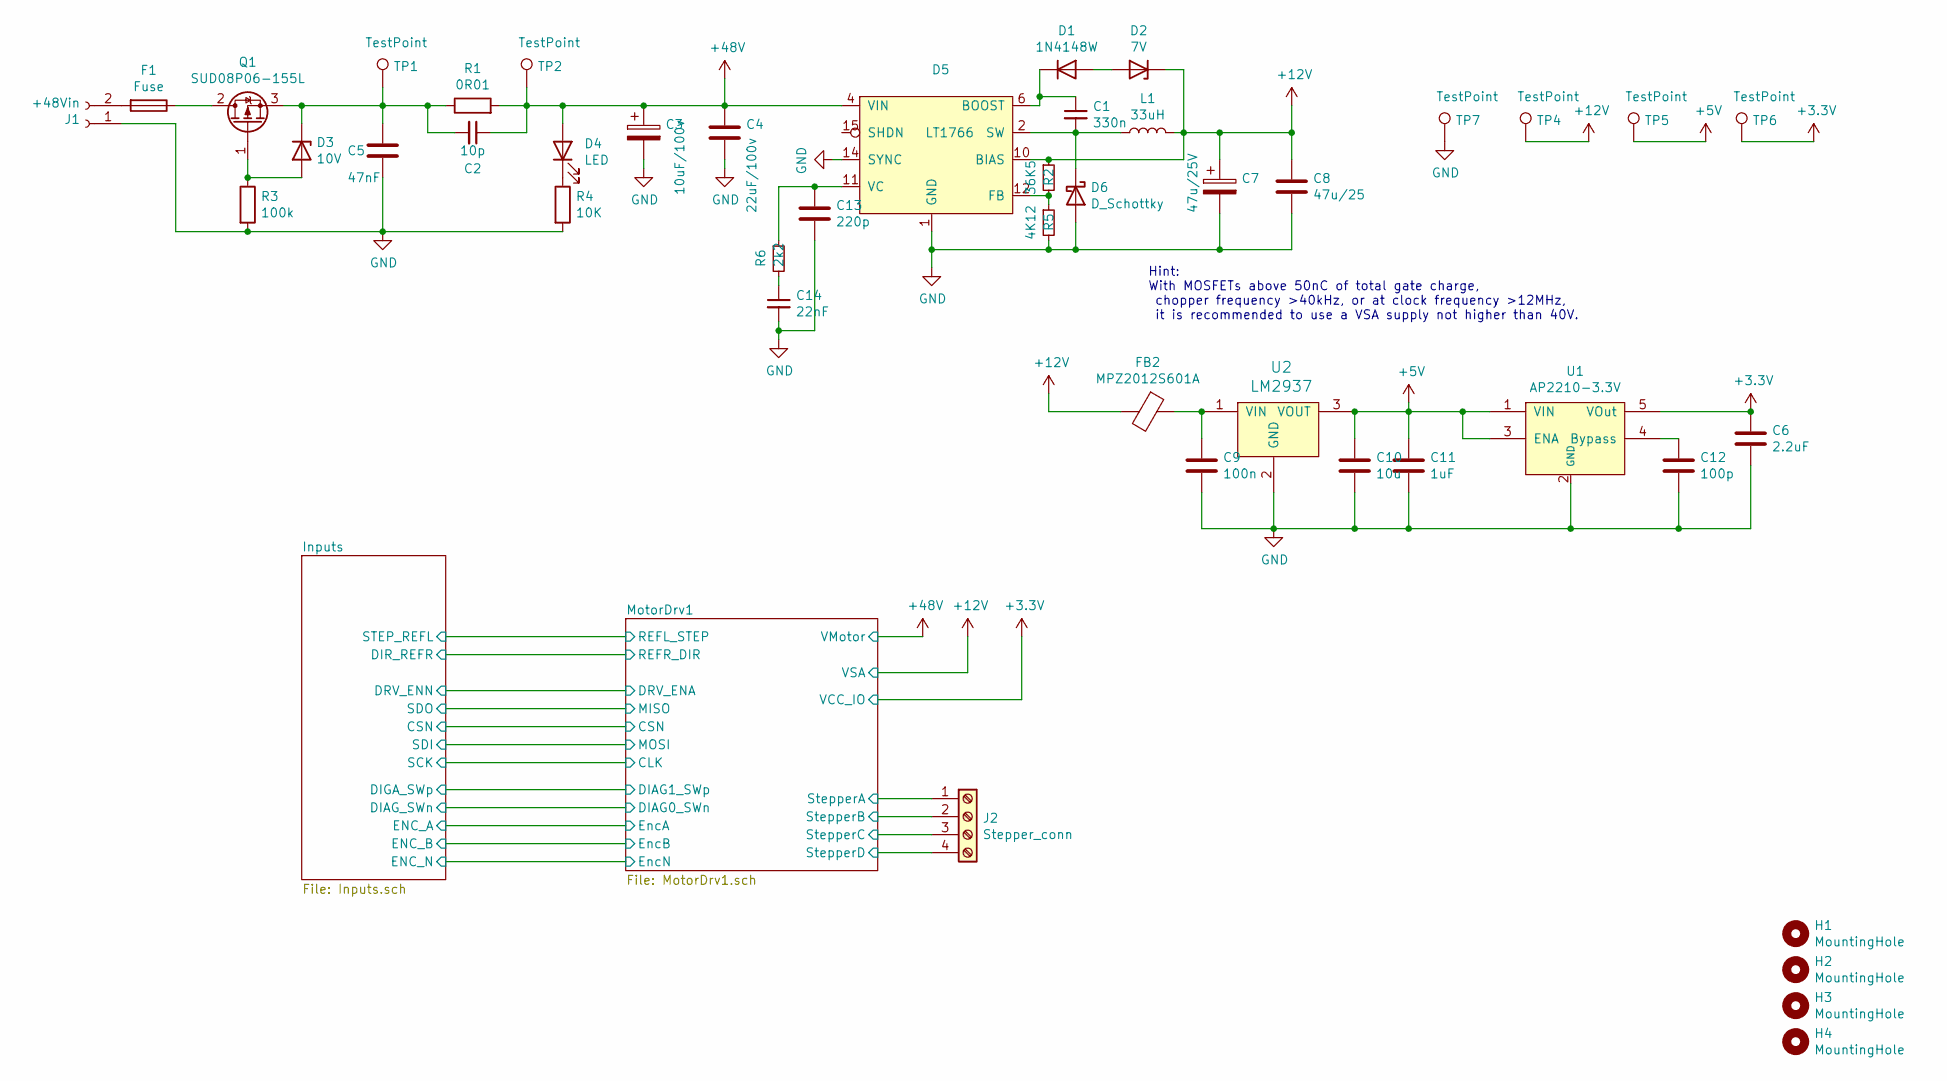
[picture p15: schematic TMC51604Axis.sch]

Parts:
C1: 330n; C_0805_peter
C2: 10p; C_0805_peter
C3: 10uF/100v; CP_Elec_8x6.2
C4: 22uF/100v; CP_Elec_8x6.2
C5: 47nF; C_0805_peter
C6: 2.2uF; C_0805_peter
C7: 47u/25V; CP_Radial_D10.0mm_P5.00mm
C8: 47u/25; C_2010_5025Metric_Pad1.52x2.65mm_HandSolder
C9: 100n; C_0603_1608Metric
C10: 10u; C_0603_1608Metric
C11: 1uF; C_0805_peter
C12: 100p; C_0805_peter
C13: 220p; C_0805_peter
C14: 22nF; C_0805_peter
D1: 1N4148W; D_SOD-123
D2: 7V; D_1206_3216Metric
D3: 10V; D_1206_3216Metric
D4: LED; D_0805_2012Metric
D5: LT1766; TSSOP-16-1EP_4.4x5mm_P0.65mm
D6: D_Schottky; D_SOD-123F
F1: Fuse; Fuse_2512_6332Metric
FB2: MPZ2012S601A; R_0805_2012Metric_Pad1.15x1.40mm_HandSolder
H1, H2, H3, H4: MountingHole; MountingHole_3.2mm_M3
J1: +48Vin; PhoenixContact_MSTB_2,5_2-GF_1x02_P5.00mm_Horizontal_Thread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
J2: Stepper_conn; TerminalBlock_Phoenix_PT-1,5-4-3.5-H_1x04_P3.50mm_Horizontal
L1: 33uH; L_7.3x7.3_H3.5
Q1: SUD08P06-155L; TO-252-2
R1: 0R01; R_2512_6332Metric
R2: 36K5; R_0805_peter
R3: 100k; R_0805_peter
R4: 10K; R_0805_peter
R5: 4K12; R_0805_peter
R6: 2k2; R_0805_peter
TP1, TP2: TestPoint; TestPoint_Pad_D1.5mm
TP4, TP5, TP6: TestPoint; TestPoint_Pad_1.5x1.5mm
TP7: TestPoint; TestPoint_THTPad_1.5x1.5mm_Drill0.7mm
U1: AP2210-3.3V; SOT-23-5_HandSoldering
U2: LM2937; SOT-223-3_TabPin2

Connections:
+5V: C10.1, C11.1, TP5.1, U1.1 (VIN), U1.3 (ENA), U2.3 (VOUT); also elsewhere on the board
+12V: C7.1, C8.1, D2.1 (K), D5.10 (BIAS), FB2.2, L1.2, R2.1, TP4.1; also elsewhere on the board
+48V: C2.1, C3.1, C4.1, D4.2 (A), D5.4 (VIN), R1.2, TP2.1; also elsewhere on the board
/MotorDrv1/StepperA: J2.1; also elsewhere on the board
/MotorDrv1/StepperB: J2.2; also elsewhere on the board
/MotorDrv1/StepperC: J2.3; also elsewhere on the board
/MotorDrv1/StepperD: J2.4; also elsewhere on the board
GND: C3.2, C4.2, C5.2, C6.2, C7.2, C8.2, C9.2, C10.2, C11.2, C12.2, C13.2, C14.2, D5.1 (GND), D5.8 (GND), D5.9 (GND), D5.14 (SYNC), D5.16 (GND), D5.17 (GND), D6.2 (A), J1.1, R3.2, R4.2, R5.2, TP7.1, U1.2 (GND), U2.2 (GND); also elsewhere on the board
unnamed: C1.1, D1.1 (K), D5.6 (BOOST)
unnamed: C1.2, D5.2 (SW), D6.1 (K), L1.1
unnamed: C2.2, C5.1, D3.1 (K), Q1.3 (S), R1.1, TP1.1
unnamed: C9.1, FB2.1, U2.1 (VIN)
unnamed: C12.1, U1.4 (Bypass)
unnamed: C13.1, D5.11 (VC), R6.1
unnamed: C14.1, R6.2
unnamed: D1.2 (A), D2.2 (A)
unnamed: D3.2 (A), Q1.1 (G), R3.1
unnamed: D4.1 (K), R4.1
unnamed: D5.12 (FB), R2.2, R5.1
unnamed: F1.1, Q1.2 (D)
unnamed: F1.2, J1.2

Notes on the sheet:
Hint: With MOSFETs above 50nC of total gate charge, chopper frequency >40kHz, or at clock frequency >12MHz, it is recommended to use a VSA supply not higher than 40V.

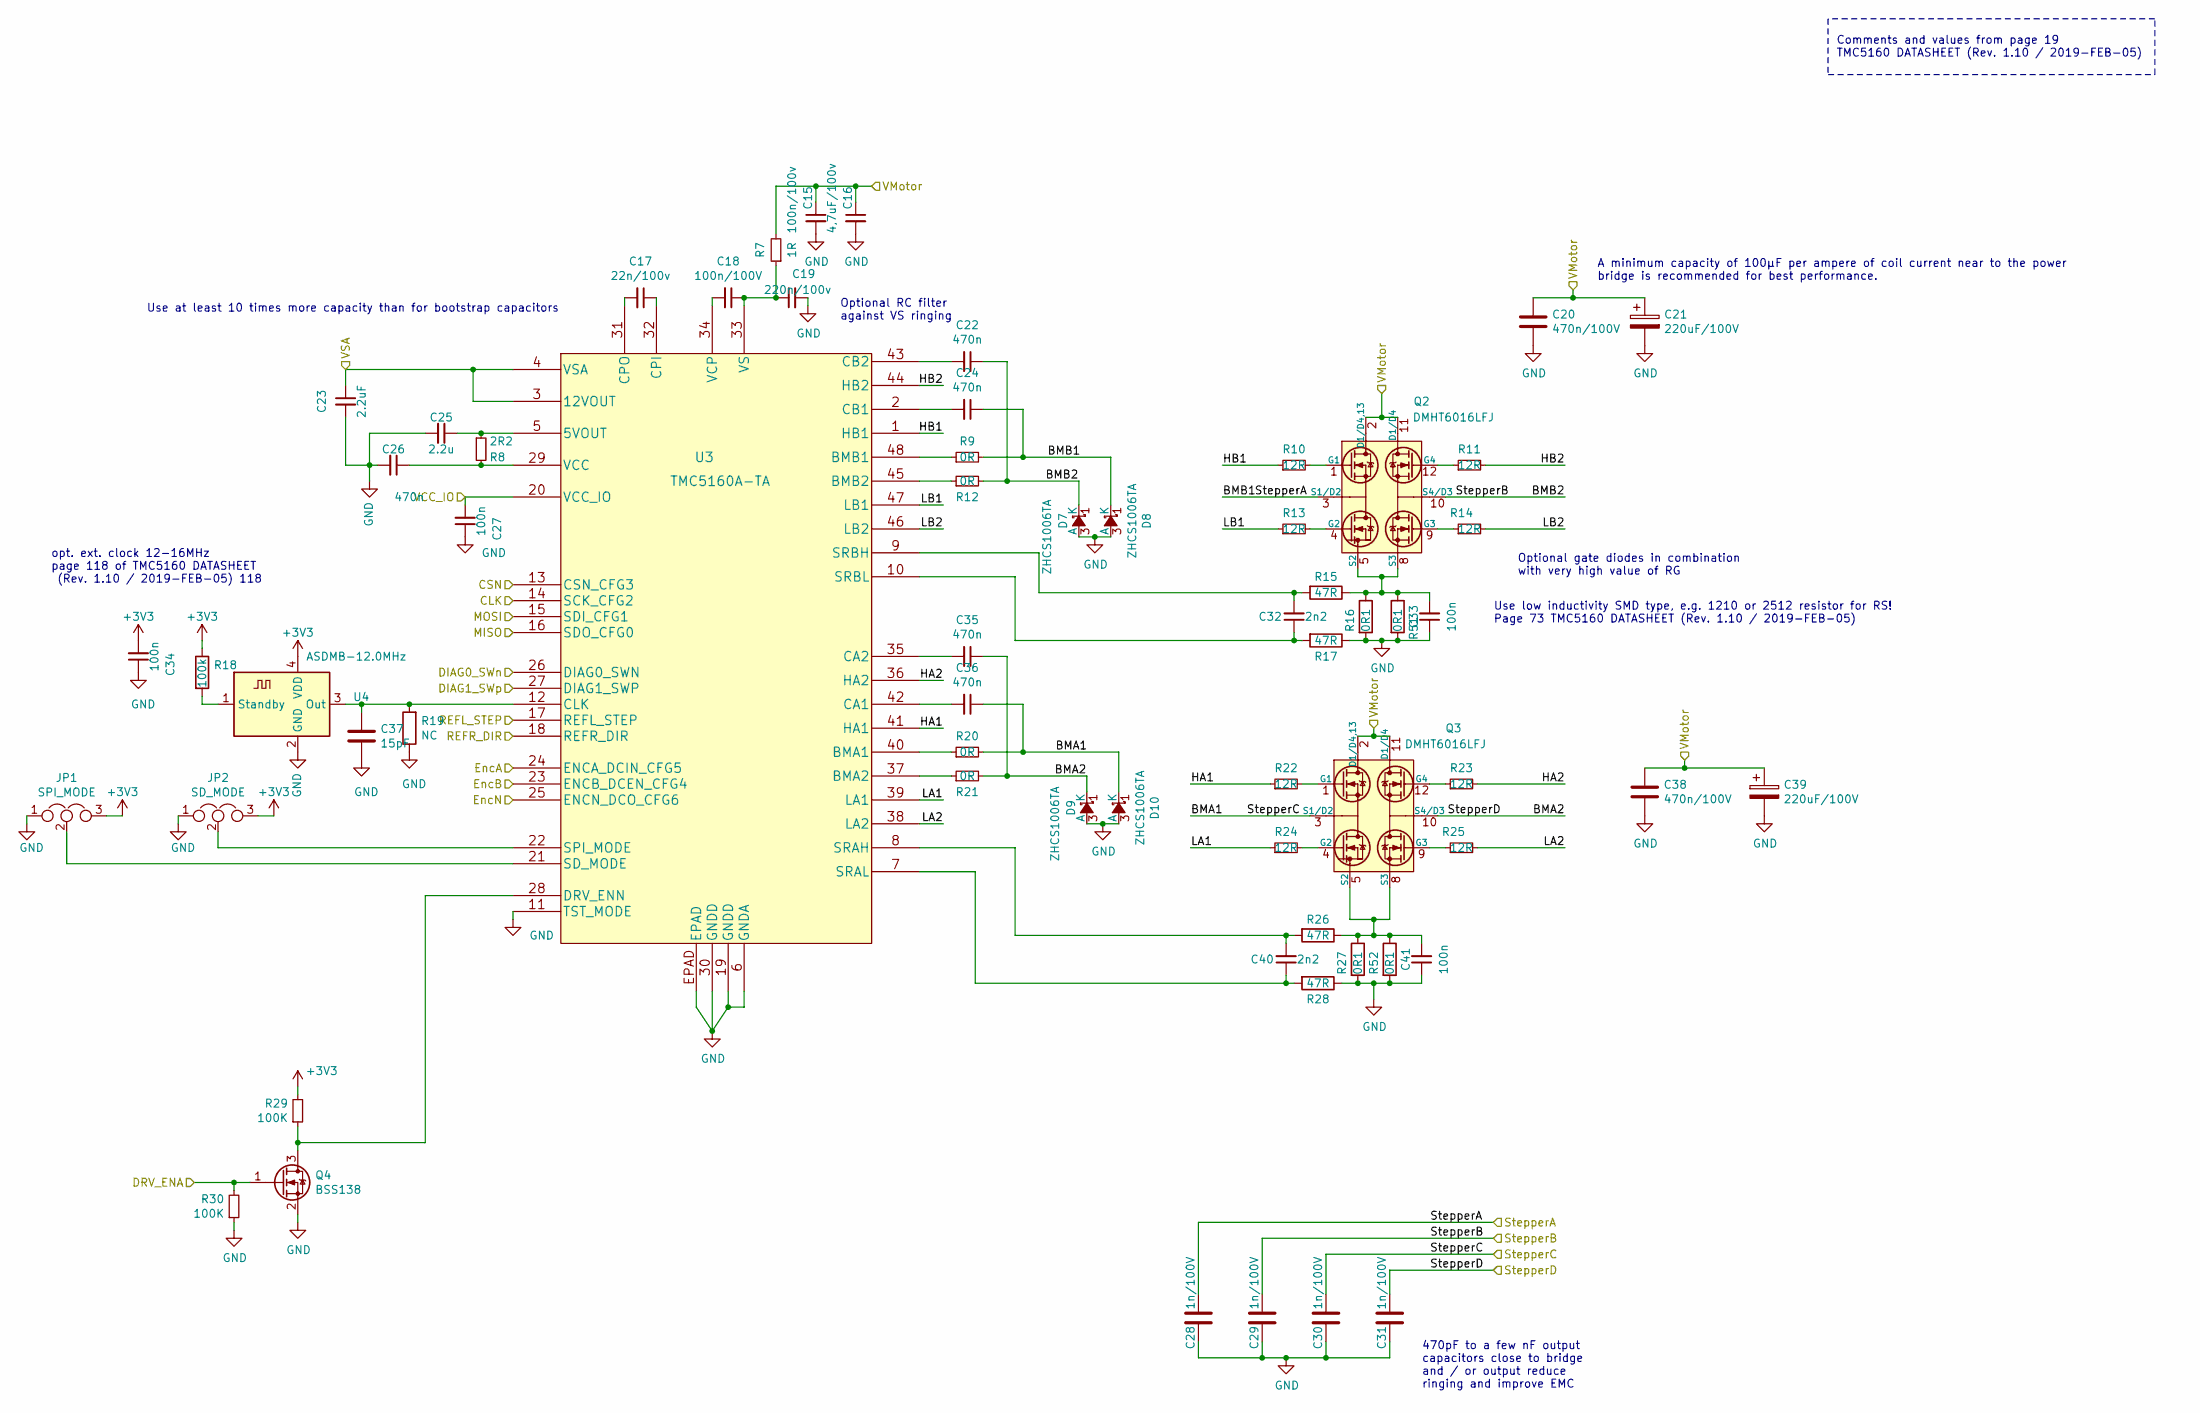
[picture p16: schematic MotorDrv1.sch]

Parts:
C15: 100n/100v; C_1210_3225Metric_Pad1.42x2.65mm_HandSolder
C16: 4,7uF/100v; C_1210_3225Metric_Pad1.42x2.65mm_HandSolder
C17: 22n/100v; C_0603_1608Metric
C18: 100n/100V; C_0805_peter
C19: 220n/100v; C_0603_1608Metric
C20, C38: 470n/100V; C_1206_3216Metric
C21, C39: 220uF/100V; CP_Elec_10x14.3
C22, C24, C26, C35, C36: 470n; C_0603_1608Metric
C23: 2.2uF; C_0603_1608Metric
C25: 2.2u; C_0603_1608Metric
C27, C33, C34, C41: 100n; C_0603_1608Metric
C28, C29, C30, C31: 1n/100V; C_0603_1608Metric
C32, C40: 2n2; C_0603_1608Metric
C37: 15pF; D_0805_peter
D7, D8, D9, D10: ZHCS1006TA; SOT-23
JP1: SPI_MODE; SolderJumper-3_P2.0mm_Open_TrianglePad1.0x1.5mm
JP2: SD_MODE; SolderJumper-3_P2.0mm_Open_TrianglePad1.0x1.5mm
Q2, Q3: DMHT6016LFJ; V-DFN5045-12
Q4: BSS138; SOT-23
R7: 1R; R_0805_peter
R8: 2R2; R_0603_1608Metric
R9, R12, R20, R21: 0R; R_0603_1608Metric
R10, R11, R13, R14, R22, R23, R24, R25: 12R; R_0603_1608Metric
R15, R17, R26, R28: 47R; R_0603_1608Metric
R16, R27, R51, R52: 0R1; R_1206_3216Metric
R18: 100k; R_0805_peter
R19: NC; R_0805_peter
R29, R30: 100K; R_0603_1608Metric
U3: TMC5160A-TA; LQFP-48-1EP_7x7mm_P0.5mm_EP3.6x3.6mm_peter
U4: ASDMB-12.0MHz; Oscillator_SMD_Abracon_ASDMB-4Pin_2.5x2.0mm

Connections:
+12V: C23.1, U3.3 (12VOUT), U3.4 (VSA); also elsewhere on the board
+48V: C15.1, C16.1, C20.1, C21.1, C38.1, C39.1, Q2.2 (D1/D4,13), Q2.11 (D1/D4), Q2.13 (D1/D4), Q3.2 (D1/D4,13), Q3.11 (D1/D4), Q3.13 (D1/D4), R7.2; also elsewhere on the board
/Inputs/CSN: U3.13 (CSN_CFG3); also elsewhere on the board
/Inputs/DIR_REFR: U3.18 (REFR_DIR); also elsewhere on the board
/Inputs/ENC_A: U3.24 (ENCA_DCIN_CFG5); also elsewhere on the board
/Inputs/ENC_B: U3.23 (ENCB_DCEN_CFG4); also elsewhere on the board
/Inputs/ENC_N: U3.25 (ENCN_DCO_CFG6); also elsewhere on the board
/MotorDrv1/CLK: U3.14 (SCK_CFG2); also elsewhere on the board
/MotorDrv1/DIAG0_SWn: U3.26 (DIAG0_SWN); also elsewhere on the board
/MotorDrv1/DIAG1_SWp: U3.27 (DIAG1_SWP); also elsewhere on the board
/MotorDrv1/DRV_ENA: Q4.1 (G), R30.2; also elsewhere on the board
/MotorDrv1/HA1: R22.1, U3.41 (HA1)
/MotorDrv1/HA2: R23.2, U3.36 (HA2)
/MotorDrv1/HB1: R10.1, U3.1 (HB1)
/MotorDrv1/HB2: R11.2, U3.44 (HB2)
/MotorDrv1/LA1: R24.1, U3.39 (LA1)
/MotorDrv1/LA2: R25.2, U3.38 (LA2)
/MotorDrv1/LB1: R13.1, U3.47 (LB1)
/MotorDrv1/LB2: R14.2, U3.46 (LB2)
/MotorDrv1/MISO: U3.16 (SDO_CFG0); also elsewhere on the board
/MotorDrv1/MOSI: U3.15 (SDI_CFG1); also elsewhere on the board
/MotorDrv1/REFL_STEP: U3.17 (REFL_STEP); also elsewhere on the board
/MotorDrv1/StepperA: C24.1, C28.1, D8.1 (K), Q2.3 (S1/D2), Q2.14 (S1/D2), R9.2; also elsewhere on the board
/MotorDrv1/StepperB: C22.1, C29.1, D7.1 (K), Q2.10 (S4/D3), Q2.15 (S4/D3), R12.2; also elsewhere on the board
/MotorDrv1/StepperC: C30.1, C36.1, D10.1 (K), Q3.3 (S1/D2), Q3.14 (S1/D2), R20.2; also elsewhere on the board
/MotorDrv1/StepperD: C31.1, C35.1, D9.1 (K), Q3.10 (S4/D3), Q3.15 (S4/D3), R21.2; also elsewhere on the board
GND: C15.2, C16.2, C19.2, C20.2, C21.2, C23.2, C25.2, C26.2, C27.1, C28.2, C29.2, C30.2, C31.2, C33.1, C34.1, C37.2, C38.2, C39.2, C41.1, D7.3 (A), D8.3 (A), D9.3 (A), D10.3 (A), JP1.1, JP2.1, Q4.2 (S), R16.2, R17.1, R19.1, R27.2, R28.1, R30.1, R51.2, R52.2, U3.6 (GNDA), U3.11 (TST_MODE), U3.19 (GNDD), U3.30 (GNDD), U3.EPAD, U4.2 (GND); also elsewhere on the board
unnamed: C17.1, U3.32 (CPI)
unnamed: C17.2, U3.31 (CPO)
unnamed: C18.1, C19.1, R7.1, U3.33 (VS)
unnamed: C18.2, U3.34 (VCP)
unnamed: C22.2, U3.43 (CB2)
unnamed: C24.2, U3.2 (CB1)
unnamed: C25.1, R8.1, U3.5 (5VOUT)
unnamed: C26.1, R8.2, U3.29 (VCC)
unnamed: C32.1, R17.2, U3.10 (SRBL)
unnamed: C32.2, R15.2, U3.9 (SRBH)
unnamed: C33.2, Q2.5 (S2), Q2.6 (S2), Q2.7 (S3), Q2.8 (S3), R15.1, R16.1, R51.1
unnamed: C35.2, U3.35 (CA2)
unnamed: C36.2, U3.42 (CA1)
unnamed: C37.1, R19.2, U3.12 (CLK), U4.3 (Out)
unnamed: C40.1, R28.2, U3.7 (SRAL)
unnamed: C40.2, R26.2, U3.8 (SRAH)
unnamed: C41.2, Q3.5 (S2), Q3.6 (S2), Q3.7 (S3), Q3.8 (S3), R26.1, R27.1, R52.1
unnamed: JP1.2, U3.21 (SD_MODE)
unnamed: JP2.2, U3.22 (SPI_MODE)
unnamed: Q2.1 (G1), R10.2
unnamed: Q2.4 (G2), R13.2
unnamed: Q2.9 (G3), R14.1
unnamed: Q2.12 (G4), R11.1
unnamed: Q3.1 (G1), R22.2
unnamed: Q3.4 (G2), R24.2
unnamed: Q3.9 (G3), R25.1
unnamed: Q3.12 (G4), R23.1
unnamed: Q4.3 (D), R29.1, U3.28 (DRV_ENN)
unnamed: R9.1, U3.48 (BMB1)
unnamed: R12.1, U3.45 (BMB2)
unnamed: R18.2, U4.1 (Standby)
unnamed: R20.1, U3.40 (BMA1)
unnamed: R21.1, U3.37 (BMA2)

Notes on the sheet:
Use at least 10 times more capacity than for bootstrap capacitors
opt. ext. clock 12-16MHz page 118 of TMC5160 DATASHEET (Rev. 1.10 / 2019-FEB-05) 118
Use low inductivity SMD type, e.g. 1210 or 2512 resistor for RS! Page 73 TMC5160 DATASHEET (Rev. 1.10 / 2019-FEB-05)
Comments and values from page 19 TMC5160 DATASHEET (Rev. 1.10 / 2019-FEB-05)
Optional gate diodes in combination with very high value of RG
Optional RC filter against VS ringing
A minimum capacity of 100µF per ampere of coil current near to the power bridge is recommended for best performance.
470pF to a few nF output capacitors close to bridge and / or output reduce ringing and improve EMC

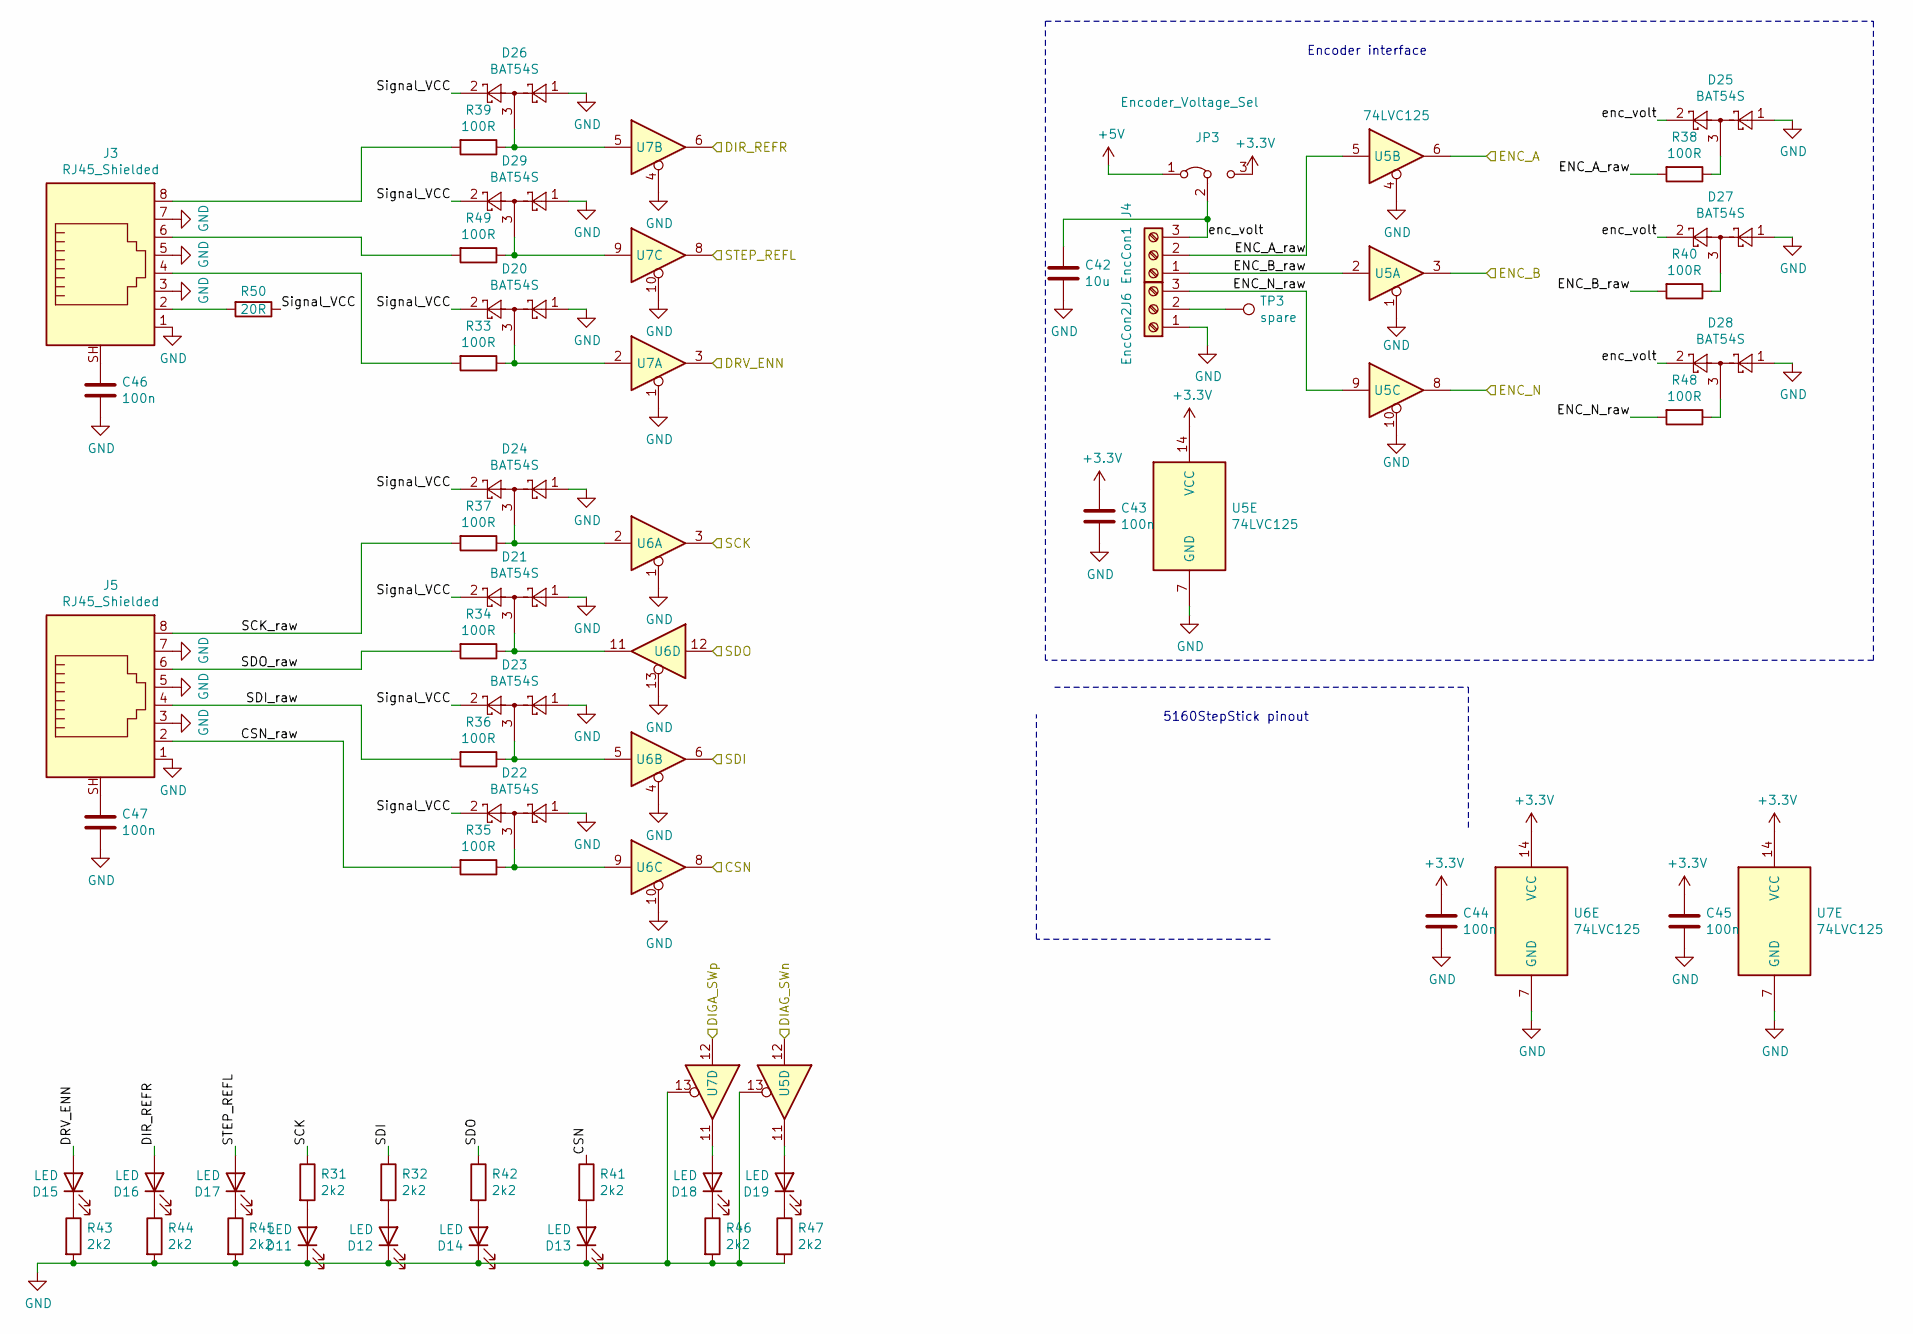
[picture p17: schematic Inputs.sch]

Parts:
C42: 10u; C_0805_peter
C43, C44, C45, C46, C47: 100n; C_0805_peter
D11, D12, D13, D14, D15, D16, D17, D18, D19: LED; D_0805__HandSolder_peter
D20, D21, D22, D23, D24, D25, D26, D27, D28, D29: BAT54S; SOT-23
J3, J5: RJ45_Shielded; 360s-1812-11001(RJ45)
J4: EncCon1; TerminalBlock_Phoenix_PT-1,5-3-3.5-H_1x03_P3.50mm_Horizontal
J6: EncCon2; TerminalBlock_Phoenix_PT-1,5-3-3.5-H_1x03_P3.50mm_Horizontal
JP3: Encoder_Voltage_Sel; SolderJumper-3_P2.0mm_Open_TrianglePad1.0x1.5mm
R31, R32, R41, R42, R43, R44, R45, R46, R47: 2k2; R_0805_peter
R33, R34, R35, R36, R37, R38, R39, R40, R48, R49: 100R; R_0805_peter
R50: 20R; R_0805_peter
TP3: spare; TestPoint_THTPad_1.0x1.0mm_Drill0.5mm
U5, U6, U7: 74LVC125; SO-14_5.3x10.2mm_P1.27mm

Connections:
+5V: JP3.1 (A); also elsewhere on the board
/Inputs/CSN: R41.1, U6.8; also elsewhere on the board
/Inputs/CSN_raw: J5.2, R35.2
/Inputs/DIR_REFR: D16.2 (A), U7.6; also elsewhere on the board
/Inputs/ENC_A: U5.6; also elsewhere on the board
/Inputs/ENC_A_raw: J4.2, R38.2, U5.5
/Inputs/ENC_B: U5.3; also elsewhere on the board
/Inputs/ENC_B_raw: J4.1, R40.2, U5.2
/Inputs/ENC_N: U5.8; also elsewhere on the board
/Inputs/ENC_N_raw: J6.3, R48.2, U5.9
/Inputs/SCK_raw: J5.8, R37.2
/Inputs/SDI_raw: J5.4, R36.2
/Inputs/SDO_raw: J5.6, R34.2
/Inputs/Signal_VCC: D20.2, D21.2, D22.2, D23.2, D24.2, D26.2, D29.2, R50.1
/Inputs/enc_volt: C42.1, D25.2, D27.2, D28.2, J4.3, JP3.2 (C)
/MotorDrv1/CLK: R31.1, U6.3; also elsewhere on the board
/MotorDrv1/DIAG0_SWn: U5.12; also elsewhere on the board
/MotorDrv1/DIAG1_SWp: U7.12; also elsewhere on the board
/MotorDrv1/DRV_ENA: D15.2 (A), U7.3; also elsewhere on the board
/MotorDrv1/MISO: R42.1, U6.12; also elsewhere on the board
/MotorDrv1/MOSI: R32.1, U6.6; also elsewhere on the board
/MotorDrv1/REFL_STEP: D17.2 (A), U7.8; also elsewhere on the board
GND: C42.2, C43.2, C44.2, C45.2, C46.2, C47.2, D11.1 (K), D12.1 (K), D13.1 (K), D14.1 (K), D20.1, D21.1, D22.1, D23.1, D24.1, D25.1, D26.1, D27.1, D28.1, D29.1, J3.1, J3.3, J3.5, J3.7, J5.1, J5.3, J5.5, J5.7, J6.1, R43.2, R44.2, R45.2, R46.2, R47.2, U5.1, U5.4, U5.7 (GND), U5.10, U5.13, U6.1, U6.4, U6.7 (GND), U6.10, U6.13, U7.1, U7.4, U7.7 (GND), U7.10, U7.13; also elsewhere on the board
unnamed: C46.1, J3.SH
unnamed: C47.1, J5.SH
unnamed: D11.2 (A), R31.2
unnamed: D12.2 (A), R32.2
unnamed: D13.2 (A), R41.2
unnamed: D14.2 (A), R42.2
unnamed: D15.1 (K), R43.1
unnamed: D16.1 (K), R44.1
unnamed: D17.1 (K), R45.1
unnamed: D18.1 (K), R46.1
unnamed: D18.2 (A), U7.11
unnamed: D19.1 (K), R47.1
unnamed: D19.2 (A), U5.11
unnamed: D20.3, R33.1, U7.2
unnamed: D21.3, R34.1, U6.11
unnamed: D22.3, R35.1, U6.9
unnamed: D23.3, R36.1, U6.5
unnamed: D24.3, R37.1, U6.2
unnamed: D25.3, R38.1
unnamed: D26.3, R39.1, U7.5
unnamed: D27.3, R40.1
unnamed: D28.3, R48.1
unnamed: D29.3, R49.1, U7.9
unnamed: J3.2, R50.2
unnamed: J3.4, R33.2
unnamed: J3.6, R49.2
unnamed: J3.8, R39.2
unnamed: J6.2, TP3.1

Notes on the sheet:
5160StepStick pinout
Encoder interface

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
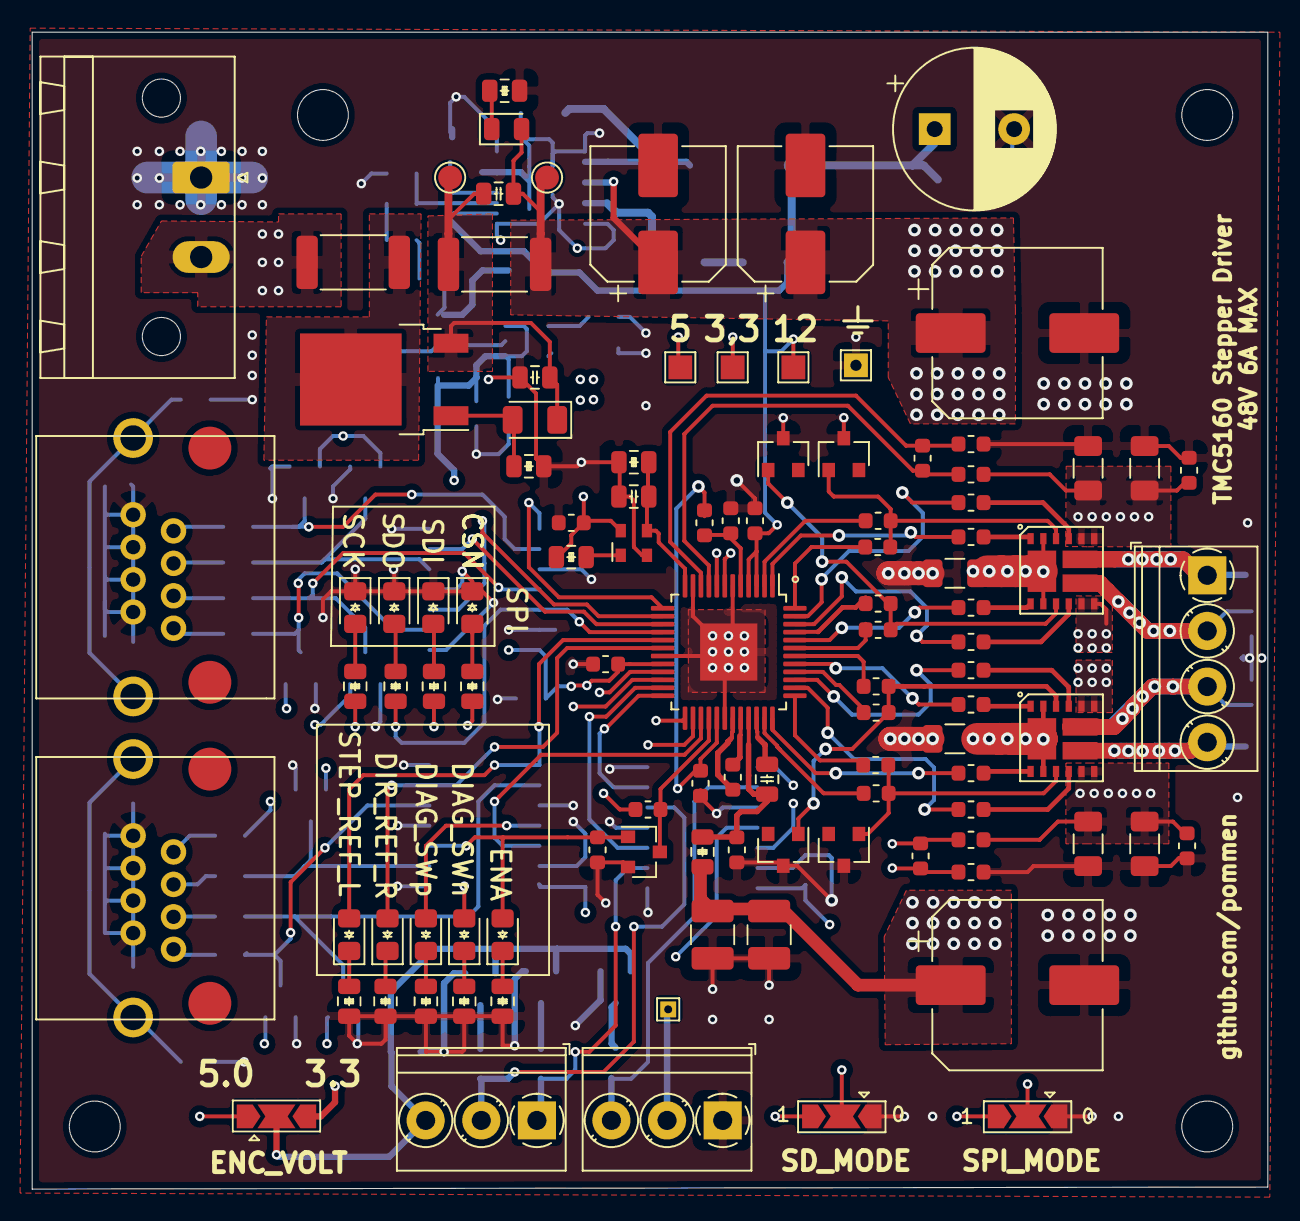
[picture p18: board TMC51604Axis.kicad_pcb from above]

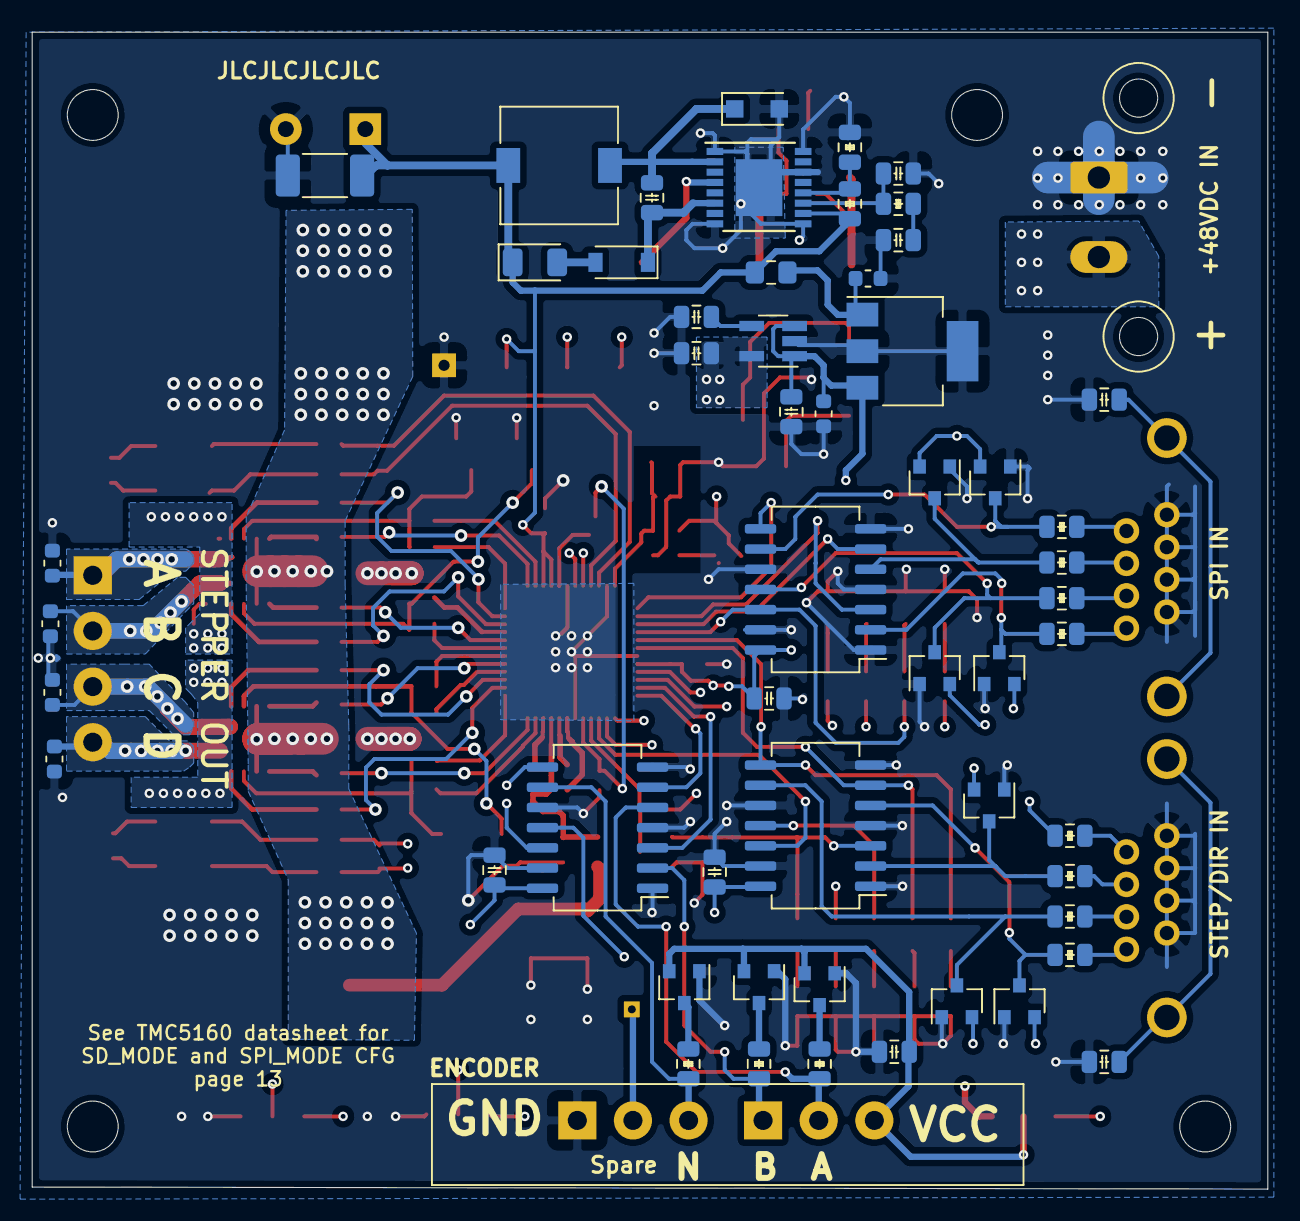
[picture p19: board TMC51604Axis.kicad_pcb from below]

Board: 4 copper layers, 77.7 x 72.8 mm, 162 parts (54 on the bottom side), 112 nets.

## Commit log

2020-05-30 Layout done! Still untested
    [Inputs.sch, MotorDrv1.sch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]
2020-05-30 Redone input section
    [Inputs.sch, MotorDrv1.sch, TMC51604Axis.kicad_pcb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]
2020-05-30 Ver0.1 done
    [TMC51604Axis.kicad_pcb, TMC51604Axis.sch]
2020-05-30 Ver 0.1 sync
    [TMC51604Axis-B_Cu.gbr, TMC51604Axis-B_Mask.gbr, TMC51604Axis-B_Paste.gbr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]
2020-06-13 Bug fixes during first assembly
    [Inputs.sch, MotorDrv1.sch, TMC51604Axis.sch]
